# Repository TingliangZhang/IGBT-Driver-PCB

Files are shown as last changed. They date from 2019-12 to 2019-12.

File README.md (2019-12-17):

FF150R12RT4 IGBT半桥驱动电路设计

张庭梁

##### 要求：

针对FF150R12RT4这款IGBT半桥模块，基于HCPL-316J光耦驱动芯片，设计一款半桥驱动电路。要求采用隔离电源，参考型号为NMH0515SC；基于光耦芯片自身特性，电路具备短路保护功能；输入电压为5V，IGBT驱动电压为正负15V。

##### 电路设计思路

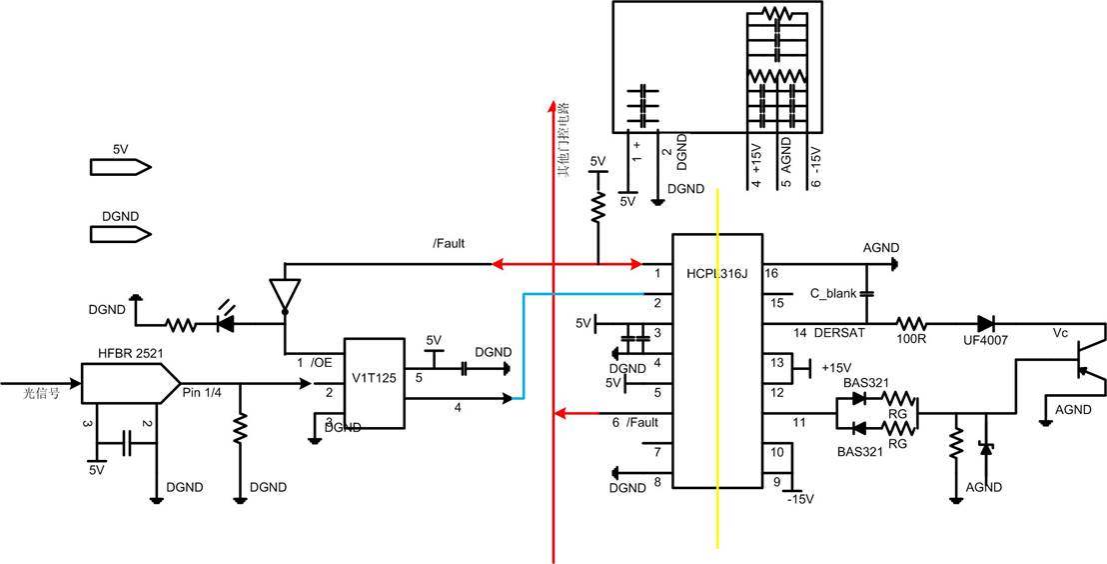
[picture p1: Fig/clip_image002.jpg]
gate drive2.jpg


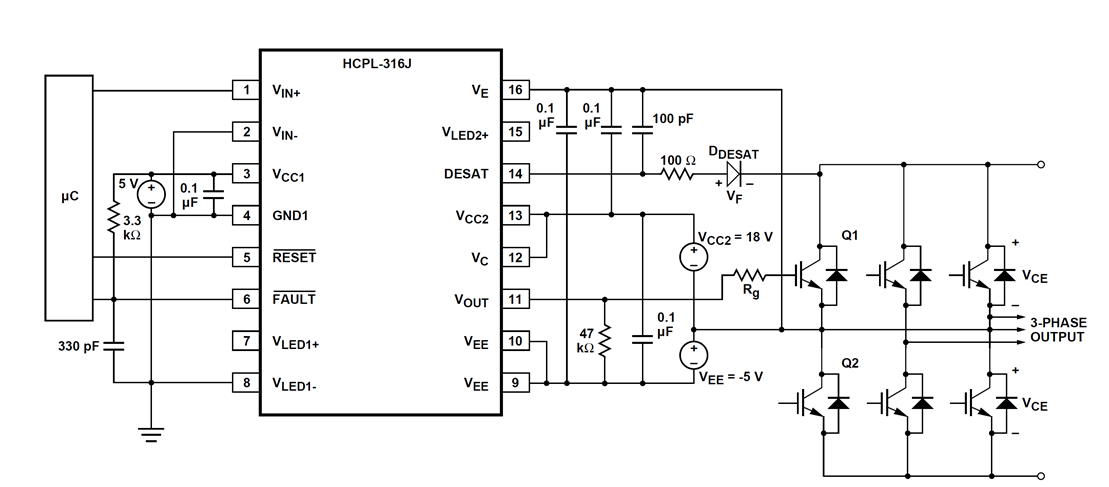
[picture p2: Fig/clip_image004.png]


Rg = 10 Ω

故障诊断电路

output pull-down resistor：下拉，安全考虑

DESAT pin protection resistor：100ohm——限流

FAULT pin capacitor：稳定纹波——防止误保护

FAULT pin pull up resistor——OC，上拉，稳定电位

二极管：UF7007——快速，压降调整

##### 原理图电路设计

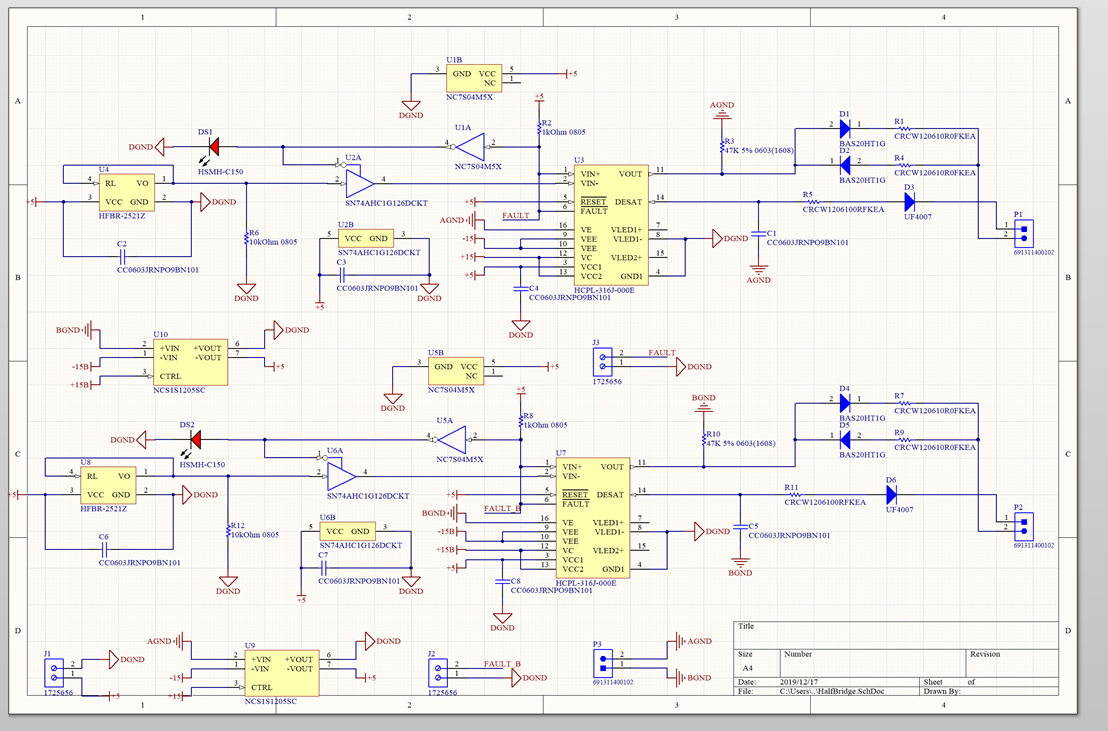
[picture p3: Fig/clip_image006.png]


注：驱动芯片用的封装NCS1S1205SC和实际使用的元件NCS1S1205SC引脚定义不一致，故按照datasheet上的引脚定义连接。在PCBdoc里面就是正确的了。

光线接受端子电路

此电路作用是接受控制电路发送的光驱动信号将其转换为电信号。电路是参考所用器件Datasheet推荐的电路。其中C1电容的作用是退耦，取值参考Datasheet。

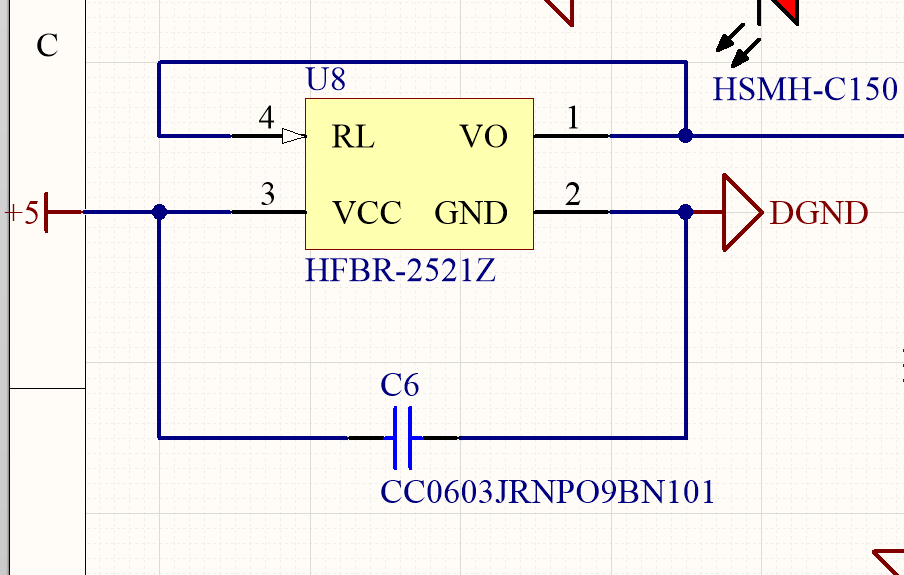
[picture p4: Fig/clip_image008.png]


光纤接受端子电路

电路主要是参考HCPL-316J-000E的Datasheet中的推荐电路进行设计

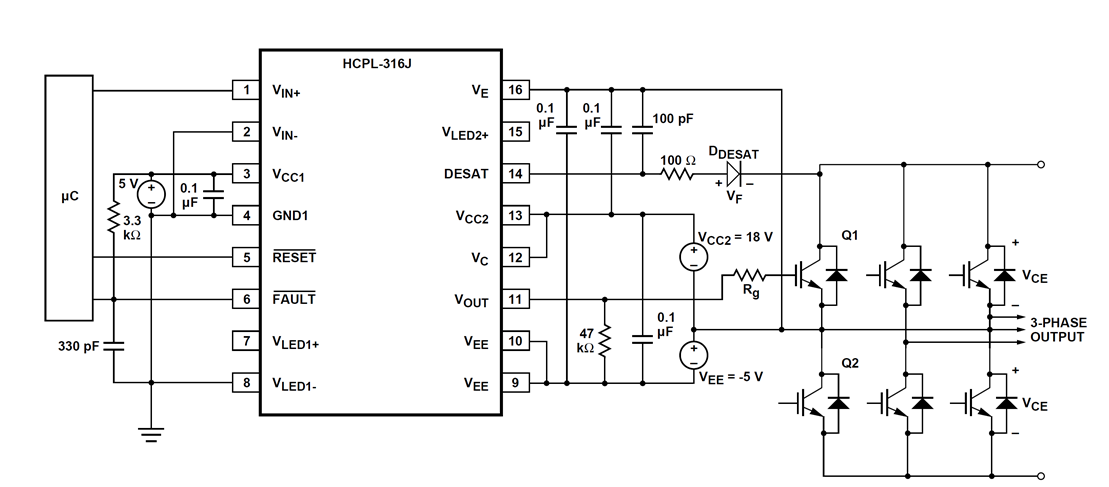
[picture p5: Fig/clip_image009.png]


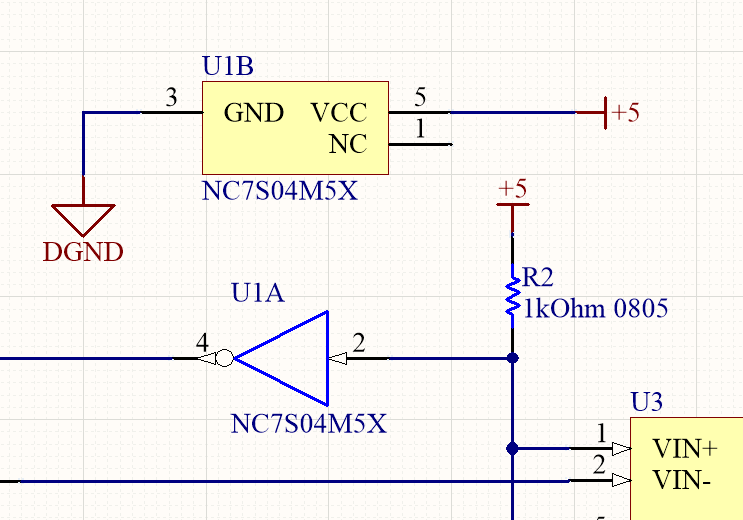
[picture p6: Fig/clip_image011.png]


反相器

 当HCPL-316J检测到故障时，其故障输出反馈段（Fault）呈现低电平，端子的前卫二极管（发光二极管）导通，然后拉低HCPL-316J的VIN+引脚输入信号，使其前卫在低电平，从而VIN-引脚上的驱动信号无法输入到HCPL-316J内，在低一时间联锁了所有ACPL-34JT的输入，使IGBT失去驱动信号从而停止工作，故达到故障保护的作用。FAULT信号的引出用于输出到板外以提示故障出现。

器件选择

| 器件 | 选型 | 备注 |
| --- | --- | --- |
| IGBT驱动芯片 | HCPL-316J | 作业要求 |
| 光纤接受端子 | HFBR2521Z | 课上ppt推荐 |
| IGBT模块 | FF150R12KS4 | 62mm封装；  半桥模块；  VCES = 1200V, Ic = 150A，  满足作业要求。 |
| 单反向门 Single Inverter Gate | NC7S04M5X | 用于实现ACPL-34JT输入驱动信号的负逻辑和缓冲； |
| 超快恢复二极管 | MURA160 | 反向耐压600V，串联可得到反向耐压1200V，实现IGBT最大工作电压1200V的目标 |
| DC-DC电源模块 | NCS1S1205SC | 5V转+-15V，以满足IGBT栅极输入电压的要求。 |
| 二极管 | BAS20HT1G | High Voltage Switching Diode, 2-Pin  SOD-323, Pb-Free, Tape and Reel  200V 500mA |
| 其他器件 | - | 参考Datasheet 的推荐值 |

三、PCB设计

本作业设计的板子所设计的板子是双层板。其布局主要分为三个部分，左边的是驱动信号，右边是驱动电压，其中右边上下分别对应上下管子的驱动。

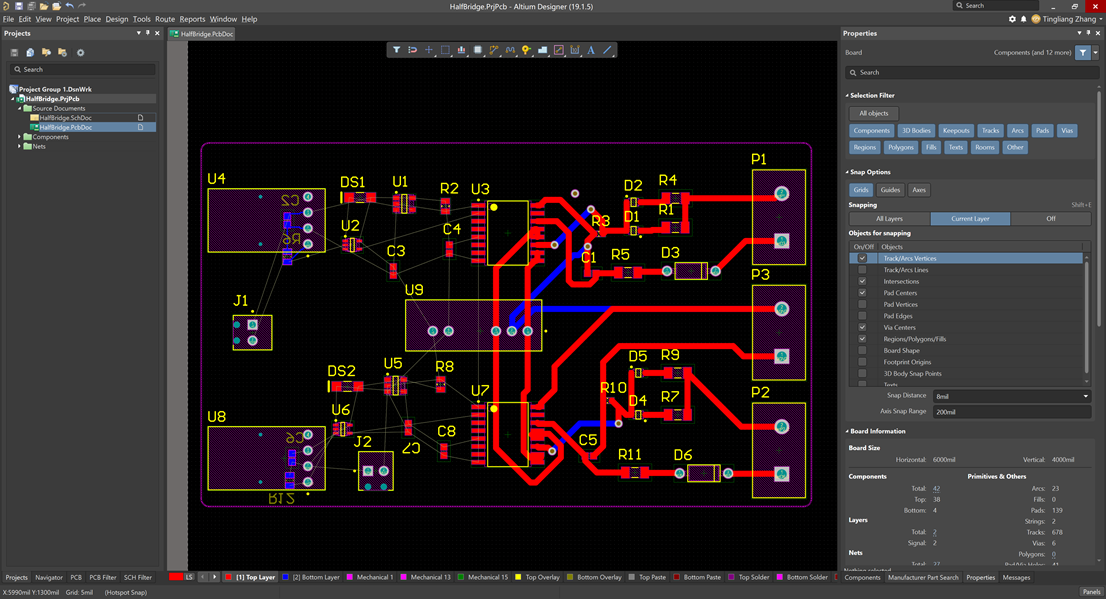
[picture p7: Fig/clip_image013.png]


强电布线

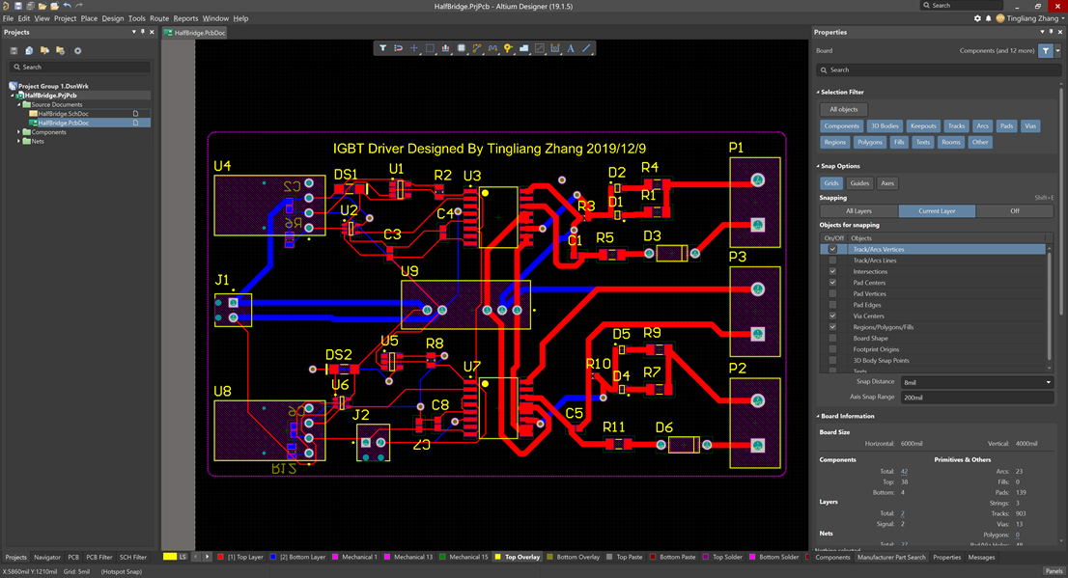
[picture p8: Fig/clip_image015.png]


弱电布局

定义外形后：

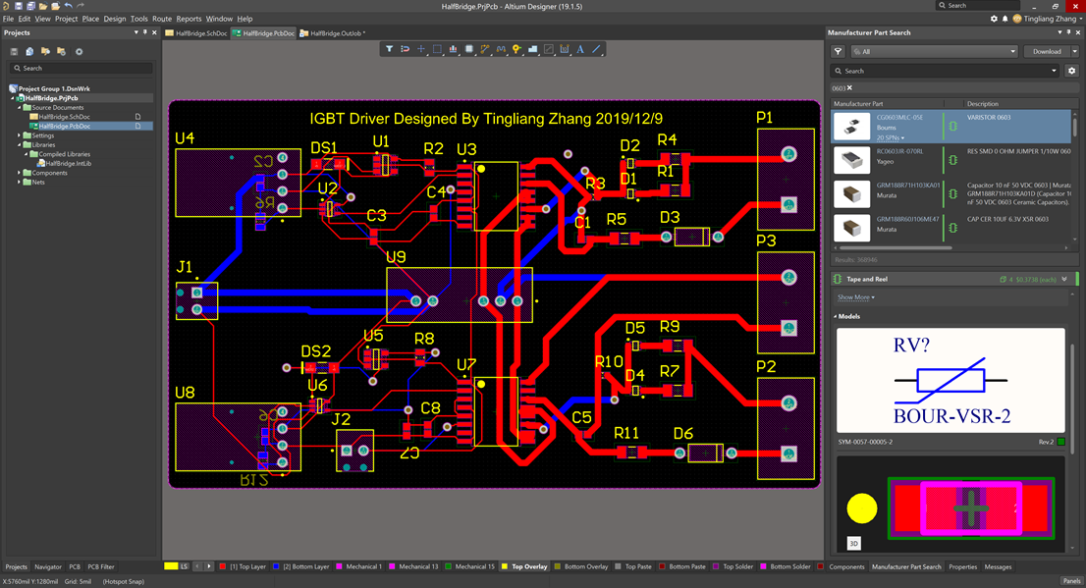
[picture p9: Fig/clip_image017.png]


铺铜之后：

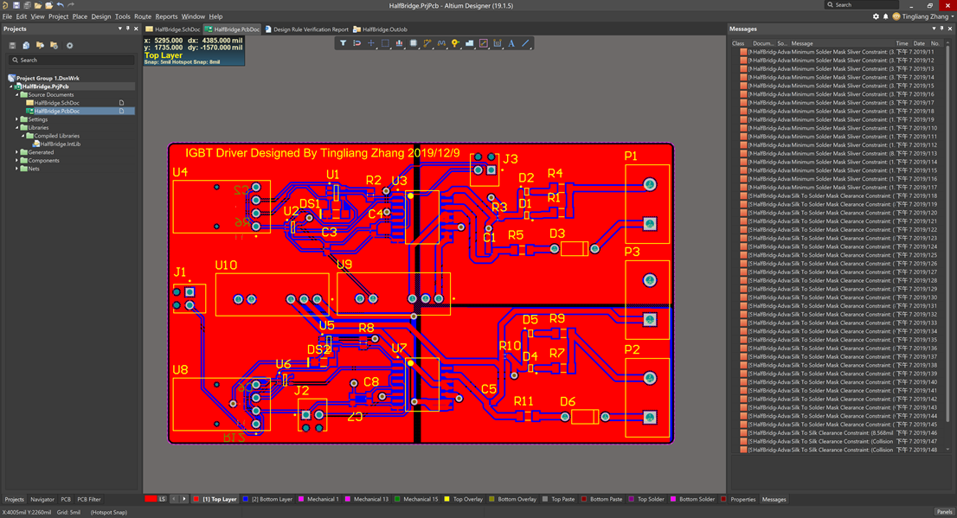
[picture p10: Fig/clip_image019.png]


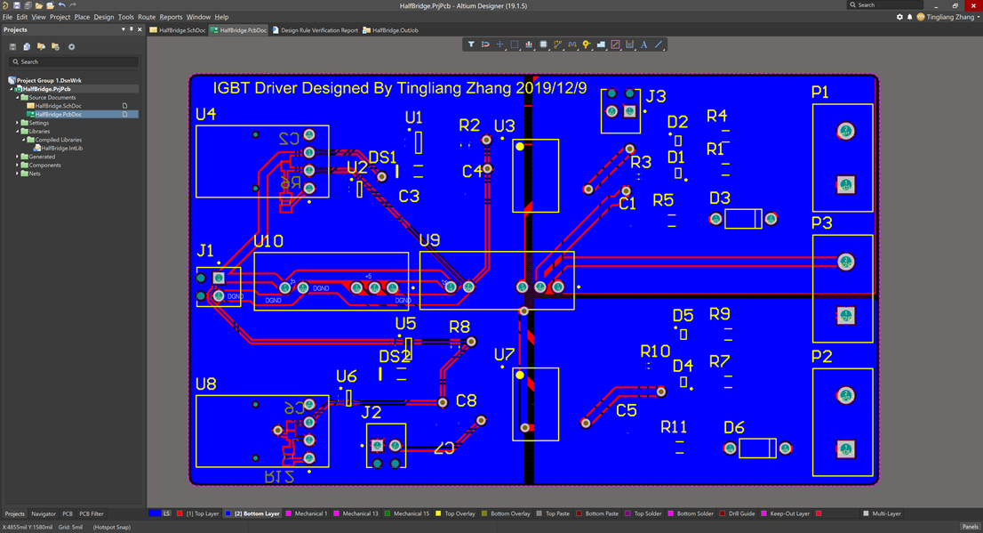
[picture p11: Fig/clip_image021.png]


3D视图：

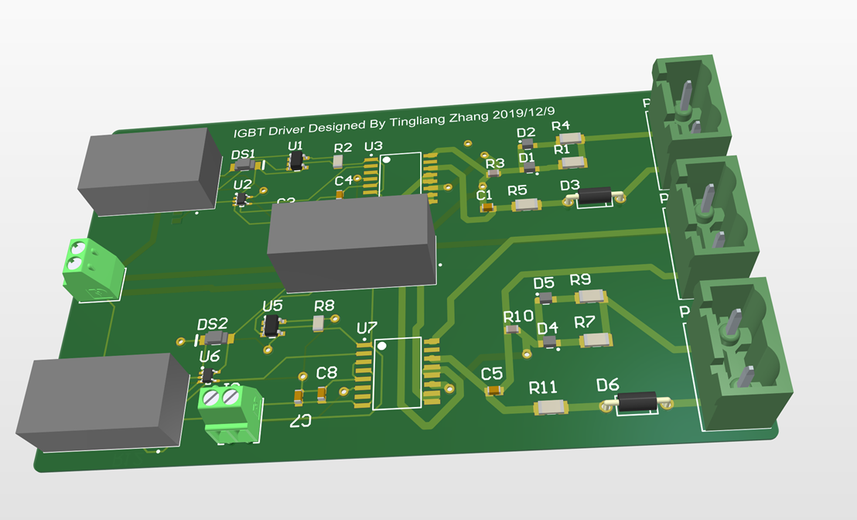
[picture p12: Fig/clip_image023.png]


V2.0更改：

上下两路+-15V驱动分离，两路驱动

光纤端子下拉电阻

故障信号低电平输出

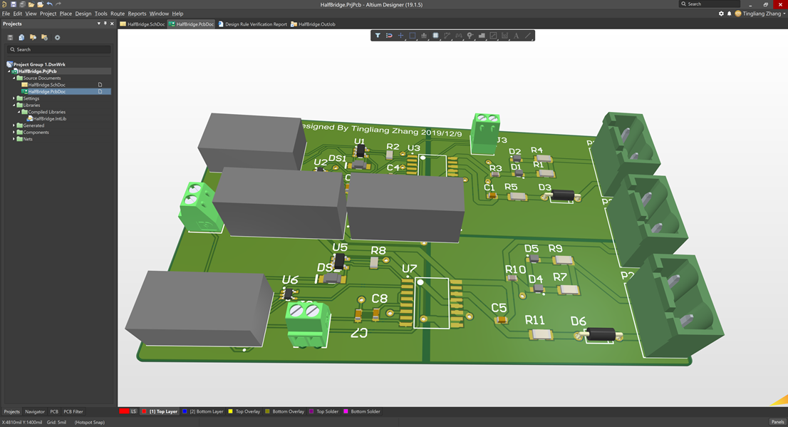
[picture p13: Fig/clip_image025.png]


一些反思：

这次布局没有搞好，强电/供电应该在一起。

同时供电和DGND可以通过铺铜连接，一开始布线可以先不考虑

Manufactured part search是个好东西。

当有更改的时候，repour all即可

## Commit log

2019-12-09 arrange components
    [HalfBridge.PcbDoc, HalfBridge.PrjPcb, HalfBridge.SchDoc]
2019-12-09 board shape
    [HalfBridge.PcbDoc, HalfBridge.PrjPcb]
2019-12-17 correct error
    [HalfBridge.PcbDoc, HalfBridge.PrjPcb, HalfBridge.SchDoc]
2019-12-17 almost finished
    [HalfBridge.PcbDoc]
